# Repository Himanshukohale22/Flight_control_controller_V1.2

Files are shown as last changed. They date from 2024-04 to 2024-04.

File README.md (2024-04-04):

# Flight_control_controller_V1.2
Hardware files for universal flight controller for small UAV's. 



### BOARD SPECIFICATION.
---

* STM32f7 cortex M4 based on board microcontroller for precision and fligt data simulation.
  * Core: Arm® 32-bit Cortex®-M7 CPU with FPU
  * Six-stage dual-issue pipeline
  • Dynamic branch prediction
  • Harvard caches (8 Kbytes of I-cache and 8 Kbytes of D-cache)
  • 64-bit AXI4 interface
  • 64-bit ITCM interface
  • 2x32-bit DTCM interfaces 
* sensors
  * MPU9250.(IMU)
    *  9-axis of freedom. (6 are used).
    * accerelometer an gyroscopic values
    * Higher calibration precision.
    * for statbility and orientation of board/vehicle.
    * configured with SPI1.
  * BMP280 .(Barometer)
    * configured with I2C .
    * barometer for altitude calculations . helps to hover the flight.
    * absolutely accurate p = 950 -- 1100 hPa.
  * NRF module
    * nrf module for communication upto 1km.
    * configured with SPI2.
  * BLE
  * WIFI
  * Servo motors
  * GPS support
  * Perhipherals
    * UART X2
    * I2C  X1
    * SPI  X1
    * CAN  X1
  * Power 
    * 3V3 sensor support
    * 5V support
    * usbB mini for testing testing.
    * jst connector i/p from 12v to 27v .
  * OSD (On screen display)
  * SD card support
  * for programme the ,board include four pins ckl , io , pwr , gnd as in 1.27mm pins(SWD). use ST-LINK.

Top Layer
---



Bottom Layer 
---


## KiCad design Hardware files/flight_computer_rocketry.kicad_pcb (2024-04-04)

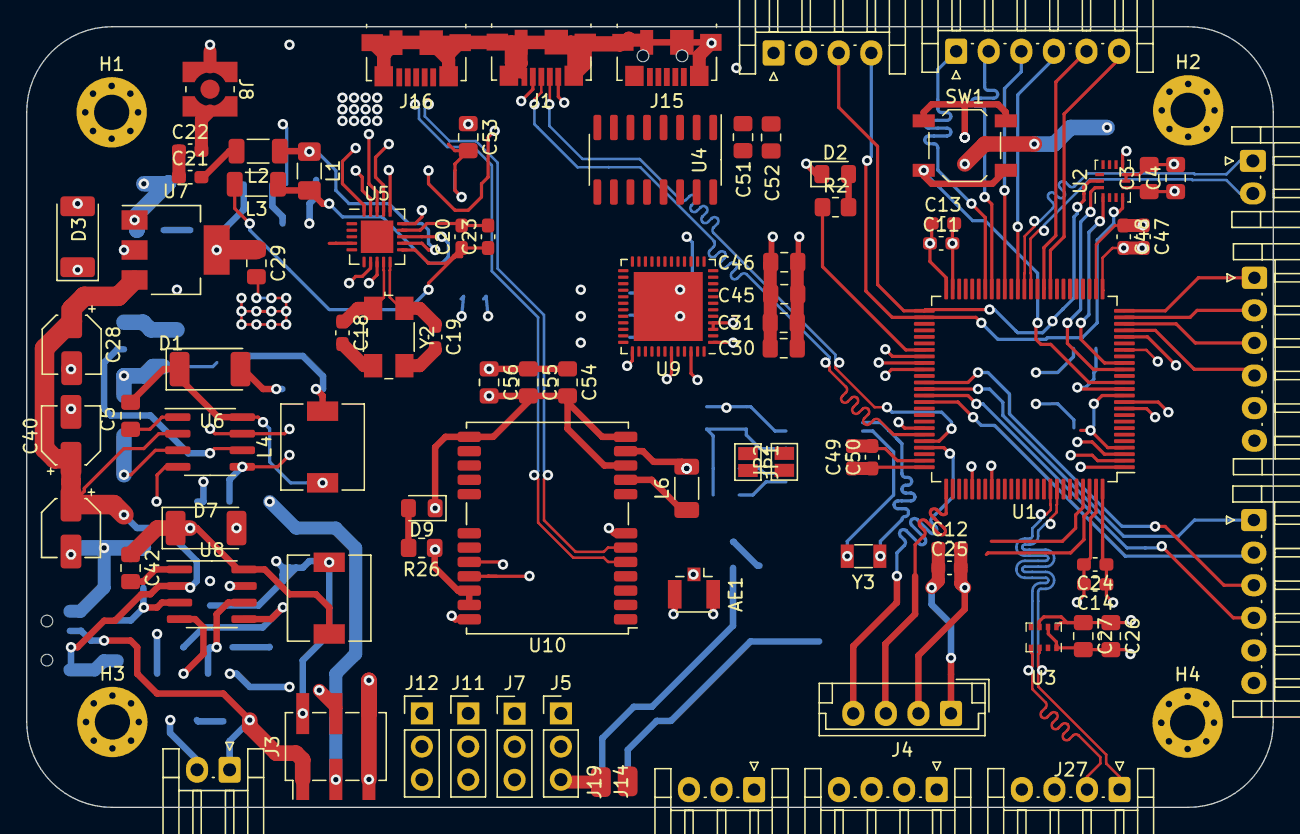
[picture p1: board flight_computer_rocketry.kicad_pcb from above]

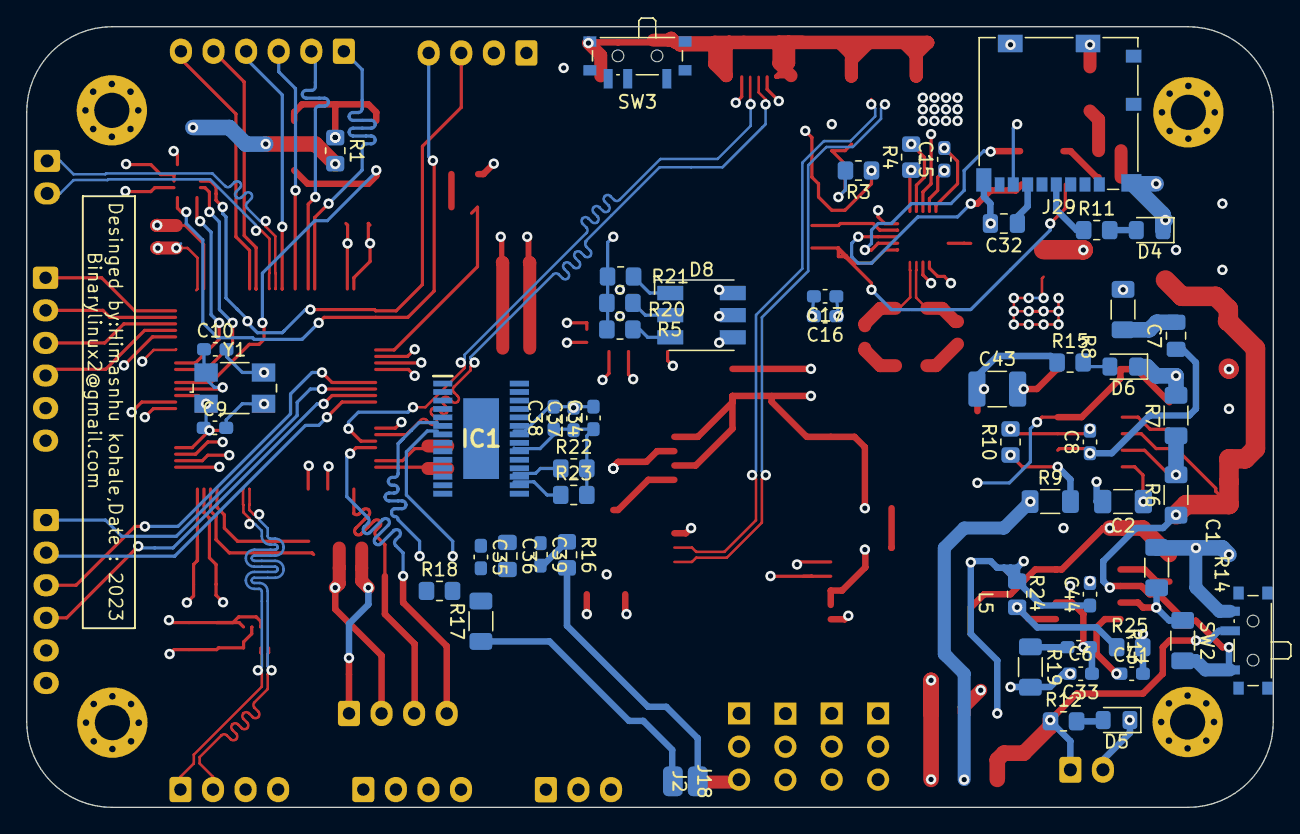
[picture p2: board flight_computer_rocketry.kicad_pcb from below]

Board: 4 copper layers, 95.6 x 59.9 mm, 145 parts (55 on the bottom side), 109 nets.

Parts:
AE1: Antenna_Chip; U.FL_Hirose_U.FL-R-SMT-1_Vertical
C1, C28, C40: 10uf; CP_Elec_4x3
C2: 8.2uf; C_1206_3216Metric_Pad1.33x1.80mm_HandSolder
C3, C4, C5, C26, C27, C30, C31, C32, C42, C45, C46, C51, C52, C53, C54, C55, C56: 100nf; C_0805_2012Metric_Pad1.18x1.45mm_HandSolder
C6: 10pf; C_0603_1608Metric_Pad1.08x0.95mm_HandSolder
C7: 1.8nf; C_0805_2012Metric_Pad1.18x1.45mm_HandSolder
C8: 68pf; C_0603_1608Metric_Pad1.08x0.95mm_HandSolder
C9, C10, C18, C19: 12pf; C_0603_1608Metric_Pad1.08x0.95mm_HandSolder
C11, C12, C13, C14, C24, C25, C44, C47, C48, C49, C50: 100pf; C_0603_1608Metric_Pad1.08x0.95mm_HandSolder
C15: 3.3nf; C_0603_1608Metric_Pad1.08x0.95mm_HandSolder
C16: 10nf; C_0603_1608Metric_Pad1.08x0.95mm_HandSolder
C17, C33: 1nf; C_0603_1608Metric_Pad1.08x0.95mm_HandSolder
C20: 22nf; C_0603_1608Metric_Pad1.08x0.95mm_HandSolder
C21: 1.5pf; C_0603_1608Metric_Pad1.08x0.95mm_HandSolder
C22: 1pf; C_0603_1608Metric_Pad1.08x0.95mm_HandSolder
C23: 4.7pf; C_0603_1608Metric_Pad1.08x0.95mm_HandSolder
C29, C36: 0.1uf; C_0805_2012Metric_Pad1.18x1.45mm_HandSolder
C34, C37, C38, C39: 0.1uf; C_0603_1608Metric_Pad1.08x0.95mm_HandSolder
C35: 22pf; C_0603_1608Metric_Pad1.08x0.95mm_HandSolder
C41: 8.2nf; C_0603_1608Metric_Pad1.08x0.95mm_HandSolder
C43: 47uf; C_1210_3225Metric_Pad1.33x2.70mm_HandSolder
D1, D3, D7: D_Zener; D_2010_5025Metric_Pad1.52x2.65mm_HandSolder
D2, D4, D5, D6, D9: blue; LED_0805_2012Metric_Pad1.15x1.40mm_HandSolder
D8: LED_RGB; LED_RGB_5050-6
H1, H2, H3, H4: MountingHole_Pad; MountingHole_2.7mm_M2.5_Pad_Via
IC1: AT7456E; SOP65P640X120-29N
J1, J15, J16: USB_B_Mini; USB_Micro-B_Molex_47346-0001
J2, J14, J18, J19: Conn_01x01_Pin; 1-PIN
J3: Conn_01x06_Pin; PinHeader_2x03_P2.54mm_Vertical_SMD
J4: Conn_01x04_Pin; JST_EH_B4B-EH-A_1x04_P2.50mm_Vertical
J5, J7, J11, J12: Conn_01x03_Pin; PinHeader_1x03_P2.54mm_Vertical
J6: Conn_01x03_Pin; JST_EH_S3B-EH_1x03_P2.50mm_Horizontal
J8: Conn_Coaxial; WR-MMCX_Wuerth_66012102111404_Vertical
J9, J27, J28: Conn_01x04_Pin; JST_EH_S4B-EH_1x04_P2.50mm_Horizontal
J10, J31, J32: Conn_01x06_Pin; JST_EH_S6B-EH_1x06_P2.50mm_Horizontal
J13, J17: Conn_01x02_Male; JST_EH_S2B-EH_1x02_P2.50mm_Horizontal
J29: Micro_SD_Card_Det2; microSD_HC_Molex_104031-0811
JP1, JP2: Jumper_2_Bridged; SolderJumper-2_P1.3mm_Open_Pad1.0x1.5mm
L1: 8.2nH; L_1206_3216Metric_Pad1.42x1.75mm_HandSolder
L2: 3.5nH; L_1206_3216Metric_Pad1.22x1.90mm_HandSolder
L3: 2.7nH; L_1206_3216Metric_Pad1.22x1.90mm_HandSolder
L4: 22uH; L_6.3x6.3_H3
L5: 29nH; L_6.3x6.3_H3
L6: 47nH; L_1206_3216Metric_Pad1.22x1.90mm_HandSolder
R1, R2, R5, R11, R12, R15, R20, R21, R25, R26: 1k; R_0805_2012Metric_Pad1.20x1.40mm_HandSolder
R3: 10K; R_0805_2012Metric_Pad1.20x1.40mm_HandSolder
R4: 22k; R_0805_2012Metric_Pad1.20x1.40mm_HandSolder
R6, R13: 169K; R_1206_3216Metric_Pad1.30x1.75mm_HandSolder
R7, R14: 13.3K; R_1206_3216Metric_Pad1.30x1.75mm_HandSolder
R8, R19: 48K; R_1206_3216Metric_Pad1.30x1.75mm_HandSolder
R9: 10k; R_1206_3216Metric_Pad1.30x1.75mm_HandSolder
R10: 1.96K; R_0805_2012Metric_Pad1.20x1.40mm_HandSolder
R16: 75R; R_0805_2012Metric_Pad1.20x1.40mm_HandSolder
R17: 150R; R_1206_3216Metric_Pad1.30x1.75mm_HandSolder
R18, R22, R23: 1K; R_0805_2012Metric_Pad1.20x1.40mm_HandSolder
R24: 8.2k; R_0805_2012Metric_Pad1.20x1.40mm_HandSolder
SW1: SW_Push_Dual_x2; SW_SPST_TL3342
SW2, SW3: SW_SPDT; SW_SPDT_PCM12
U1: STM32F722VCTx; LQFP-100_14x14mm_P0.5mm
U2: BMI160; Bosch_LGA-14_3x2.5mm_P0.5mm
U3: BMP280; Bosch_LGA-8_2x2.5mm_P0.65mm_ClockwisePinNumbering
U4: CH340G; SOIC-16_3.9x9.9mm_P1.27mm
U5: NRF24L01; QFN-20-1EP_4x4mm_P0.5mm_EP2.5x2.5mm
U6, U8: TPS54233; SOIC-8_3.9x4.9mm_P1.27mm
U7: AMS1117-3.3; SOT-223-3_TabPin2
U9: ESP32-PICO-D4; QFN-48-1EP_7x7mm_P0.5mm_EP5.3x5.3mm
U10: NEO-8Q; ublox_NEO
Y1: Crystal_GND23_Small; Crystal_SMD_0603-4Pin_6.0x3.5mm
Y2: Crystal_GND23; Crystal_SMD_0603-4Pin_6.0x3.5mm
Y3: Crystal; Crystal_SMD_3215-2Pin_3.2x1.5mm

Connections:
3V3: C3.1, C4.1, C11.1, C12.1, C13.1, C14.1, C16.1, C17.1, C24.1, C25.1, C26.1, C27.1, C30.1, C31.1, C45.1, C46.1, C47.1, C48.1, C49.1, C50.1, C51.1, C52.1, C53.2, C54.1, C55.1, C56.1, J3.4, J4.1, J9.3, J16.1 (VBUS), J27.3, J29.4 (VDD), R3.2, R11.1, R26.1, U1.6 (VBAT), U1.11 (VDD), U1.21 (VDDA), U1.27 (VDD), U1.50 (VDD), U1.75 (VDD), U1.100 (VDD), U2.5 (VDDIO), U2.8 (VDD), U3.6 (VDDIO), U3.8 (VDD), U4.4 (V3), U4.16 (VCC), U5.7 (VDD), U5.15 (VDD), U5.18 (VDD), U9.1 (VDDA), U9.3 (VDDA3P3), U9.4 (VDDA3P3), U9.19 (VDD3P3_RTC), U9.37 (VDD3P3_CPU), U9.43 (VDDA), U9.46 (VDDA), U10.7 (VDD_USB), U10.22 (V_BCKP), U10.23 (VCC)
5V: C34.1, C37.1, C38.1, C43.1, IC1.3 (DVDD), IC1.19 (~RESET), IC1.21 (AVDD), IC1.24 (PVDD), J3.3, J6.2, J31.5, J32.5, L4.2, R9.1, R15.1, R18.2, R22.2, R23.2
9V: C44.1, J3.2, J5.2, J7.2, J11.2, J12.2, L5.2, R24.1
+3.3V: C29.1, D3.1 (K), U7.2 (VO)
AGND: AE1.2 (PCB_Trace), C1.2, C2.2, C3.2, C4.2, C8.2, C9.2, C10.2, C11.2, C12.2, C13.2, C14.2, C15.2, C16.2, C17.2, C18.2, C19.2, C20.2, C22.2, C23.2, C24.2, C25.2, C26.2, C27.2, C28.2, C29.2, C30.2, C31.2, C32.2, C33.2, C34.2, C37.2, C38.2, C40.2, C41.2, C43.2, C44.2, C45.2, C46.2, C47.2, C48.2, C49.2, C50.2, C51.2, C52.2, C53.1, C54.2, C55.2, C56.2, D1.2 (A), D2.1 (K), D3.2 (A), D4.1 (K), D5.1 (K), D6.1 (K), D7.2 (A), D9.1 (K), H1.1, H2.1, H3.1, H4.1, IC1.4 (DGND), IC1.20 (AGND), IC1.23 (PGND), J1.5 (GND), J1.6 (Shield), J3.5, J3.6, J4.2, J5.3, J6.3, J7.3, J8.2 (Ext), J9.4, J11.3, J12.3, J15.5 (GND), J15.6 (Shield), J16.5 (GND), J16.6 (Shield), J17.2, J19.1, J27.4, J29.7 (DAT0), J29.11 (SHIELD), J31.6, J32.6, R1.2, R4.2, R5.2, R7.2, R8.2, R10.2, R14.2, R19.2, R20.2, R21.2, R25.2, SW2.3 (C), SW3.1 (A), U1.10 (VSS), U1.19 (VSSA), U1.26 (VSS), U1.49 (VSS), U1.74 (VSS), U1.99 (VSS), U2.6 (GNDIO), U2.7 (GND), U3.1 (GND), U3.7 (GND), U4.1 (GND), U5.8 (VSS), U5.14 (VSS), U5.17 (VSS), U5.20 (VSS), U6.7 (GND), U7.1 (GND), U8.7 (GND), U9.49 (GND), U10.10 (GND), U10.12 (GND), U10.13 (GND), U10.24 (GND), Y1.2, Y1.3, Y2.2, Y2.3
COMP: C7.1, C8.1, U6.6 (COMP)
COMP_9V: C6.1, C33.1, U8.6 (COMP)
CONTROL_LED: R2.1, U1.57 (PD10)
CS_SPI1: IC1.8 (~CS), J29.2 (DAT3/CD), U1.28 (PA4), U5.2 (CSN)
CS_SPI2: J28.4, U1.52 (PB13), U2.4 (INT1)
D+: J15.3 (D+), U4.5 (UD+)
D-: J15.2 (D-), U4.6 (UD-)
HS: IC1.18 (~HSYNC), R22.1
I2C1+: J27.2, U1.92 (PB6), U3.4 (SCK)
I2C1-: J27.1, U1.93 (PB7), U3.3 (SDI)
LED_BLUE: D8.6 (RA), U1.58 (PD11)
LED_GREEN: D8.5 (GA), U1.59 (PD12)
LED_RED: D8.4 (BA), U1.60 (PD13)
LOS: IC1.12 (LOS), R18.1
M1: J31.4, U1.22 (PA0)
M2: J31.3, U1.23 (PA1)
M3: J31.2, U1.24 (PA2)
M4: J31.1, U1.25 (PA3)
M5: J32.4, U1.64 (PC7)
M6: J32.1, U1.63 (PC6)
M7: J32.2, U1.65 (PC8)
M8: J32.3, U1.62 (PD15)
MISO_SPI1: IC1.11 (SDOUT), J29.3 (CMD), U1.30 (PA6), U5.5 (MISO)
MISO_SPI2: J28.1, U1.17 (PC2), U2.1 (SDO)
MOSI_SPI1: IC1.9 (SDIN), J29.8 (DAT1), U1.31 (PA7), U5.4 (MOSI)
MOSI_SPI2: J28.2, U1.16 (PC1), U2.14 (SDx)
unnamed: C6.2, R19.1
unnamed: C7.2, R8.1
unnamed: C21.2, L2.2
unnamed: C35.2, C36.2, R17.2
unnamed: C39.2, R16.1
unnamed: C5.1, D1.1 (K), L4.1, U6.8 (PH)
unnamed: D2.2 (A), R2.2
unnamed: D4.2 (A), R11.2
unnamed: D5.2 (A), R12.2
unnamed: D6.2 (A), R15.2
unnamed: C42.1, D7.1 (K), L5.1, U8.8 (PH)
unnamed: D8.3 (BK), R5.1
unnamed: D8.2 (GK), R20.1
unnamed: D8.1 (RK), R21.1
unnamed: D9.2 (A), R26.2
unnamed: IC1.5 (CLKIN), Y3.2
unnamed: C35.1, IC1.25 (SAG)
unnamed: C39.1, IC1.22 (VIN)
unnamed: C36.1, IC1.26 (VOUT)
unnamed: IC1.6 (XFB), Y3.1
unnamed: J2.1, R17.1
unnamed: C21.1, C22.1, J8.1 (In)
unnamed: J18.1, R16.2
unnamed: C32.1, J29.6 (VSS)
unnamed: R1.1, SW1.1 (C)
unnamed: SW1.2 (D), U1.14 (NRST)
unnamed: SW3.2 (B), U1.94 (BOOT0)
unnamed: R3.1, SW3.3 (C)
unnamed: C9.1, U1.12 (PH0), Y1.1
unnamed: C10.1, U1.13 (PH1), Y1.4
unnamed: L1.1, L2.1, U5.12 (ANT1)
unnamed: L1.2, L3.1, U5.13 (ANT2)
unnamed: C15.1, U5.19 (DVDD)
unnamed: R4.1, U5.16 (IREF)
unnamed: C20.1, C23.1, L3.2, U5.11 (VDD_PA)
unnamed: C5.2, U6.1 (BOOT)
unnamed: R6.2, R7.1, U6.3 (EN)
unnamed: R9.2, R10.1, U6.5 (FB)
unnamed: C2.1, U6.4 (SS)
unnamed: C42.2, U8.1 (BOOT)
unnamed: R13.2, R14.1, U8.3 (EN)
unnamed: R24.2, R25.1, U8.5 (FB)
unnamed: C41.1, U8.4 (SS)
PPM_CAM: J6.1, U1.53 (PB14)
PWM1: J10.6, U1.34 (PB0)
PWM2: J10.5, U1.35 (PB1)
PWM3: J10.4, U1.39 (PE9)
PWM4: J10.3, U1.41 (PE11)
PWM5: J10.2, U1.43 (PE13)
PWM6: J10.1, U1.44 (PE14)
RF_IN: AE1.1 (FEED), L6.2, U10.11 (RF_IN)
RXDP_ESP: JP1.1 (A), U4.3 (RXD), U9.40 (U0RXD/IO3)
RXDP_ESP_TO_STM32: JP2.2 (B), U1.97 (PE0)
SCK_SPI1: IC1.10 (SCLK), J29.5 (CLK), U1.29 (PA5), U5.3 (SCK)
SCK_SPI2: J28.3, U1.51 (PB12), U2.13 (SCx)
SERVO_1: J5.1, U1.1 (PE2)
SERVO_2: J7.1, U1.2 (PE3)
SERVO_3: J11.1, U1.3 (PE4)
SERVO_4: J12.1, U1.4 (PE5)
SYS_JTCK_SWCLK: J4.3, U1.76 (PA14)
SYS_JTMS_SWDIO: J4.4, U1.72 (PA13)
TXDP_ESP: JP2.1 (A), U4.2 (TXD), U9.41 (U0TXD/IO1)
TXDP_ESP_TO_STM32: JP1.2 (B), U1.98 (PE1)
UART5_RX: J9.2, U1.83 (PD2), U10.20 (TXD/SPI_MISO)
UART5_TX: J9.1, U1.80 (PC12), U10.21 (RXD/SPI_MOSI)
UART7+: J13.2, U1.37 (PE7)
UART7-: J13.1, U1.38 (PE8)
USB_+: J1.3 (D+), U1.70 (PA11)
USB_-: J1.2 (D-), U1.71 (PA12)
USB_GPS+: J16.3 (D+), U10.5 (USB_DM)
USB_GPS-: J16.2 (D-), U10.6 (USB_DP)
USB_ID: J1.4 (ID), U1.69 (PA10)
VCC_RF: L6.1, U10.9 (VCC_RF)
VIN: J1.1 (VBUS), J3.1, J17.1, R12.1, SW2.2 (B)
VIN_TO_PARA: C1.1, C28.1, C40.1, R6.1, R13.1, SW2.1 (A), U6.2 (VIN), U7.3 (VI), U8.2 (VIN)
VS: IC1.17 (~VSYNC), R23.1
cr+: C18.1, U5.9 (XC2), Y2.1
cr-: C19.1, U5.10 (XC1), Y2.4
